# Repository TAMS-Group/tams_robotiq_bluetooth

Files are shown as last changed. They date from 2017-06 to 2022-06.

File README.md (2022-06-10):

# Serial Bluetooth Connection for Robotique Gripper and FT Sensor

Since some robotic arms, like the UR5 do not provide a communication connection inside, it is necessary to lay the cables for connected grippers or sensors on the outside of the arm. This leads to entanglement and to unintented contact with other objects. We created a device which can be installed at the end of the arm and which provides multiple bluetooth connections, thus making the cables unnecessary.

The device is designed for the use of a UR5 with a Robotiq gripper and/or FT sensor but it can easily be altered for other arms and grippers.

installed device

The installed device between the gripper and the FT sensor.

The device consits of two 3D printed parts. One is holding all electronics and one is a simple lid. The electronics are described in the following part.
Up to two Bluetooth connections can be established which is necessary because the Robotiq gripper and FT sensor have the same ID but different baudrates and can therefore not be on the same bus.

## Electronics

Each Bluetooth connection is provided by a chain of a HC-05, a teensy 3.2 and a RS-485 converter. The teensy is serial connected the other two chips and handles the forwarding of bytes in both directions. The necessary code can be found [**here**](code).
Power is provided by the UR5 as 48V. A converter is needed since the gripper and sensor need 24V. Furthermore, 5V are needed for the electronics. Therefore two converters are integrated which provide 24V and 5V. The connections are shown below.

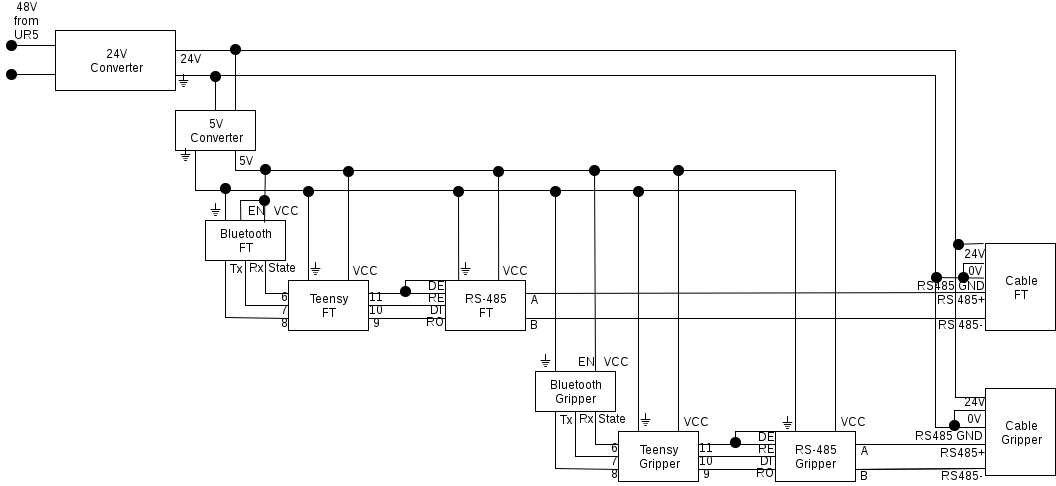
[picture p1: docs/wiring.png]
circuit diagram


In order to save space, the two teensy and the RS-485 converters are soldered together as a pair. The HC-05 are not soldered together to prevent interferance. 
**Make sure that you programmed the HC-05 using the AT commands before you solder them (see next section).**

## Programming the HC-05

The HC-05 is programmed using AT commands. To be able to use them, we have to enter the AT mode. Do this by holding the button during power up. The LED should blink slowly afterwards. Now connect the HC-05 to a teensy and use the [**code**](code/at.arduino) to be able to send the AT commands. 

Open the seriel monitor with 9600 baud using both line endings. 

Test connection by sending only **AT**. The HC-05 should response with **OK**.

Now get the Bluetooth adress by using **AT+ADDR?**. Write it down, we will need it later.

Set the name to something usefull (linke "gripper") by using **AT+NAME=<Param>**.

Set the password by using **AT+PSWD=<Param>**.

Set the baudrate by using **AT+UART=<Param>,<Param2>,<Param3>**. Param1 is the baudrate, it should be 115200 for the gripper and 19200 for the sensor. Param2 is the stop bit, it has to be 0 for both. Param3 is the parity bit, it has to be 0 for both.

The HC-05 should now be programmed. Reconnect it to the power without holding the button to get it back into normal mode.

## 3D Printed Case

The case should be printed with enough infill (>=30%), since it has to be strong enough. We used ABS as material which worked very well but you can also try PLA if you want.
When assembling, first put all electronics inside. The planned positions of the chips are shown below. Then put the lid on it and use the vertical screws to connect the device to the FT sensor. Afterwards, put the gripper on top of it and use the horizontal screws to fix it.

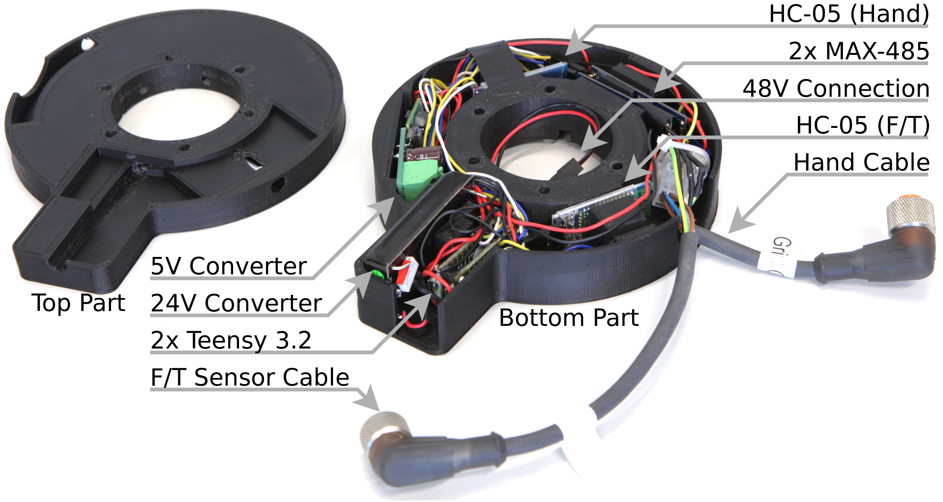
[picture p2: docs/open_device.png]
assembyl


## Serial Connection

With Linux it is possible to establish a serial connection via Bluetooth using **rfcomm**. First pair and trust the HC-05 with your computer (you can use blueman-manager if you want). Then bind the HC-05 to seriel devices using **rfcomm bind /dev/rfcomm1 BTADRESS**, where BTADRESS is your bluetooth adress which you noted during programming of the HC-05. You can also see it in the blueman-manager.
Do the same for the second HC-05 to /dev/rfcomm2 and remember which rfcomm is connected to which device.
Should you ever run into problems, use **rfcomm release all** to remove all seriel connections and then bind them again. You can see the current status using **rfcomm -a**.
If you want to send manual bytes over the serial connection for testing, you can use **minicom**.
Flash the [**test sketch**](code/test.arduino) on the teensy to test the connection. All incomming data from bluetooth will be displayed on the serial monitor.
 
## Installation of the FT sensor, Bluetooth adapter, and the Robotiq Gripper
  
1. connect FT sensor to the square FT adapter, which is mounted to the UR5 end-effector link
   - tighten 4 screws on the outer ring of the FT sensor with Metric screwdriver
   - the top cylinder on the UR5 wrist 3 should align with the top cylinder on the FT sensor

2. connect the Bluetooth device with the FT sensor
   - connect the black-red cable of the device to the exposed black-red cable from the UR5 end-effector
   - put the top part of the device align with the top cylinder of the FT sensor, see [figure](docs/installed_device.png)
   - tighten the 6 screws on the device with Metric screwdriver

3. connect the gripper with the Bluetooth device
   - put the gripper in the correct position (the COM and PWR port side should be at the left side wrt the top side of the FT sensor)
   - tighten the 6 screws, whose holes are on the curved surface of the device, by Imperial screwdriver (the yellow set, 7/64 size)

4. connect two cables coming from the Bluetooth device to the FT sensor and the gripper
   - the longer cable goes to the FT sensor, the shorter one goes to the PWR  port of the gripper
  
## Troubleshooting
- Make sure that your user has the correct rights, i.e. beeing in group dialout
- In TAMS, pair the bluetooth first (password: 1234), then use `sudo rfcomm bind /dev/rfcomm1 98:D3:31:50:16:50` and `sudo rfcomm bind /dev/rfcomm2 98:D3:31:60:18:35`
- To run these two commands while start up, copy the following codes into `/etc/rc.local`.
```
sudo rfcomm bind /dev/rfcomm1 98:D3:31:50:16:50
sudo rfcomm bind /dev/rfcomm2 98:D3:31:60:18:35
exit 0
```
- If you still have error, make sure that the Bluetooth adapter of the computer is as near as possible to the robotic arm and that it is not obstructed by anything.
- If the bluetooth connection stops to work, try **rfcomm release all** and rebinding of the devices.
- If you update your system to `ubuntu 18.04`, the default version of pymodbus install from `apt-get` does not work, use `pip install pymodbus==1.2.0` to downgrade it to version 1.2.0 in your local install.
 - However, in Ubuntu 20.04, we need to use python3, and in python3 we cannot use pymodbus 1.2.0 as pymodbus was modified to fit python3 after version 1.3.0, so we grab the code of pymodbus 1.2.0 to our robotiq package, and make it work in python3. Now just install pymodbus via `sudo apt install python3-pymodbus` is fine.
- If you have any further errors (or problem solutions), please write issues or edit this file directly.

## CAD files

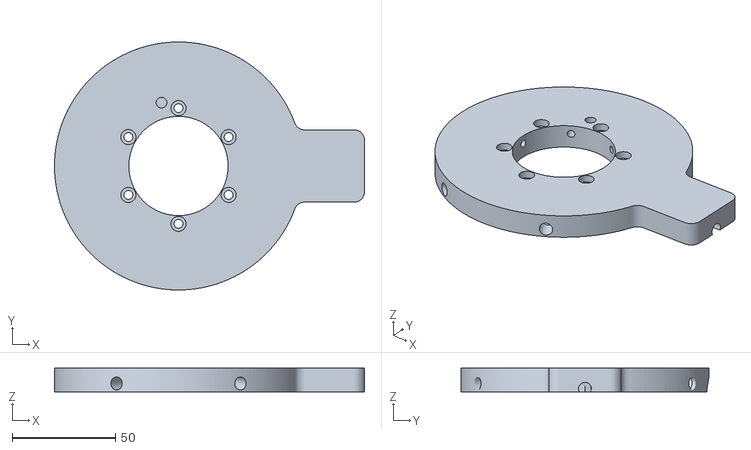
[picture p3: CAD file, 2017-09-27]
cad/top.stl
150.0 x 120.0 x 11.5

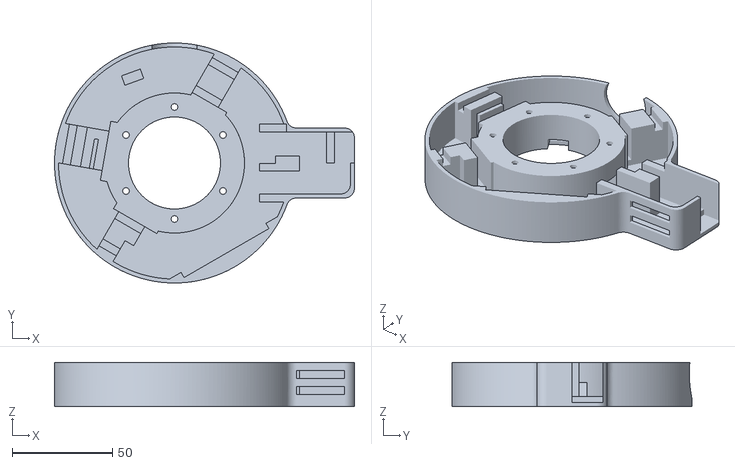
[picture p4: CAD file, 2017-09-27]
cad/bottom.stl
150.0 x 120.0 x 22.0

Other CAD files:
cad/bottom.ipt
cad/top.ipt

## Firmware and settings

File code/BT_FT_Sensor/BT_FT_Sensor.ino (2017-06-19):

// This sketch is for the teensy which connects to the Robotiq FT sensor
// Make sure that you connected the pins as they are definded in this code


#define RS_PIN 11 //pin for setting read write status on RS485 converter

bool debug;
int last_write_time;

void setup(){
  debug = false; // activate output to the serial monitor
  writing = false;
  
  pinMode(RS_PIN, OUTPUT);  
  digitalWrite(RS_PIN, writing);
  
  Serial.begin(19200);   // For the Arduino IDE Serial Monitor  
  Serial3.begin(19200); // for the rs-485 bus
  Serial2.begin(19200); //bluetooth
  delay(5000);
  Serial.println("Beginning bluetooth to RS-485. Please set debug to true if you want more output on the serial monitor.");

}


void loop(){
  digitalWrite(RS_PIN, writing); // set the rs-485 on read or write, depending on the current state

  if (Serial3.available()){ //data from bluetooth
    digitalWrite(RS_PIN, true);
    char c = Serial3.read();
    Serial2.write(c);
    if (debug){
      Serial.println("");
      Serial.println("");
      Serial.print("blu ");      
      Serial.print(c, HEX);
    }
    last_write_time = micros();       
    writing = true; 
  }else if(writing && micros() - last_write_time > 2000){
    writing = false;
  }
  
  if (Serial2.available()){ //data from hand
    char c = Serial2.read();        
    Serial3.write(c);
    if(debug){
      Serial.println("");
      Serial.print("hand ");  
      Serial.print(c,HEX);
    }    
  }
}

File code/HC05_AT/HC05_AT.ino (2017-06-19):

// This code is based on the "YourDuino.com Example: BlueTooth HC-05 Setup"
// Make sure that you started the HC-05 in AT mode by holding the button during start up
 
void setup()
{
  Serial.begin(9600);   // For the Arduino IDE Serial Monitor
  delay(5000);
  Serial.println("Enter AT commands in top window.");
  Serial3.begin(38400); // HC-05 default speed in AT command mode

}


void loop()
{
  // READ from HC-05 and WRITE to Arduino Serial Monitor
  if (Serial3.available())
    Serial.write(Serial3.read());

  // READ Arduino Serial Monitor and WRITE to HC-05
  if (Serial.available()){
    //char c = Serial.read();
    Serial3.write(Serial.read());
    //Serial.write(c);
  }  
}

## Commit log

2017-06-21 added wiring
2017-09-27 added cad files
    [bottom.ipt, bottom.stl, top.ipt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]
2021-08-07 add installation process of the FT sensor, bluetooth device and the gripper in README
